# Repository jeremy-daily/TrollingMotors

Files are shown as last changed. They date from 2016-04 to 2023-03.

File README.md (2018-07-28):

# TrollingMotors
A project that runs 2 trolling motors on a boat with multiple microcontrollers on a CAN bus.

## Operation
Pressing the green button lets you change mode with an up and down of the joystick.

The red button stops the motor and sends the system into mode 0, which is off.

### Mode 0: OFF

### Mode 1: Normal 

### Mode 2: Figure 8

### Mode 3: Full

### Mode 4: Calibrate Compass

## Servos
Use the following Arduino pins on the Teensy 3.2

D23 is the left motor.

D16 is the right motor.

The motor controller is a VEX Victor SP that takes inputs generated by the Servo library. The value of 92 is neutral on the controllers.

## CAN Message
This section describes the interpretation and value for each of the CAN messages on the trolling motor system. All nodes are running at 500k CAN with 11-bit IDs.
### Control Message
* ID: 0x700
* Length: 1
* Meaning
  * Bit 0: upButtonState
  * Bit 1: downButtonState
  * Bit 2: leftButtonState
  * Bit 3: rightButtonState
  * Bit 4: pushButtonState
  * Bit 5: doubleClick
  * Bit 6: redButtonState
  * Bit 7: greenButtonState
  
This is the message sent by the Joystick or other controller every 25 ms. 

### Mode Message
* ID: 0x201
* Length: 2
* Meaning
  * Byte 0: number of modes of operation
  * Byte 1: current mode number

This messages is sent by the main controller as an informational message.
  
### Display Message 1
* ID: 0x211
* Length: 8

All bytes are ascii characters to be displayed on the upper left character slots of a 16X2 character display.

### Display Message 2
* ID: 0x212
* Length: 8

All bytes are ascii characters to be displayed on the upper right character slots of a 16X2 character display.

### Display Message 3
* ID: 0x221
* Length: 8
 
All bytes are ascii characters to be displayed on the lower left character slots of a 16X2 character display.

### Display Message 4
* ID: 0x222
* Length: 8

All bytes are ascii characters to be displayed on the lower right character slots of a 16X2 character display.

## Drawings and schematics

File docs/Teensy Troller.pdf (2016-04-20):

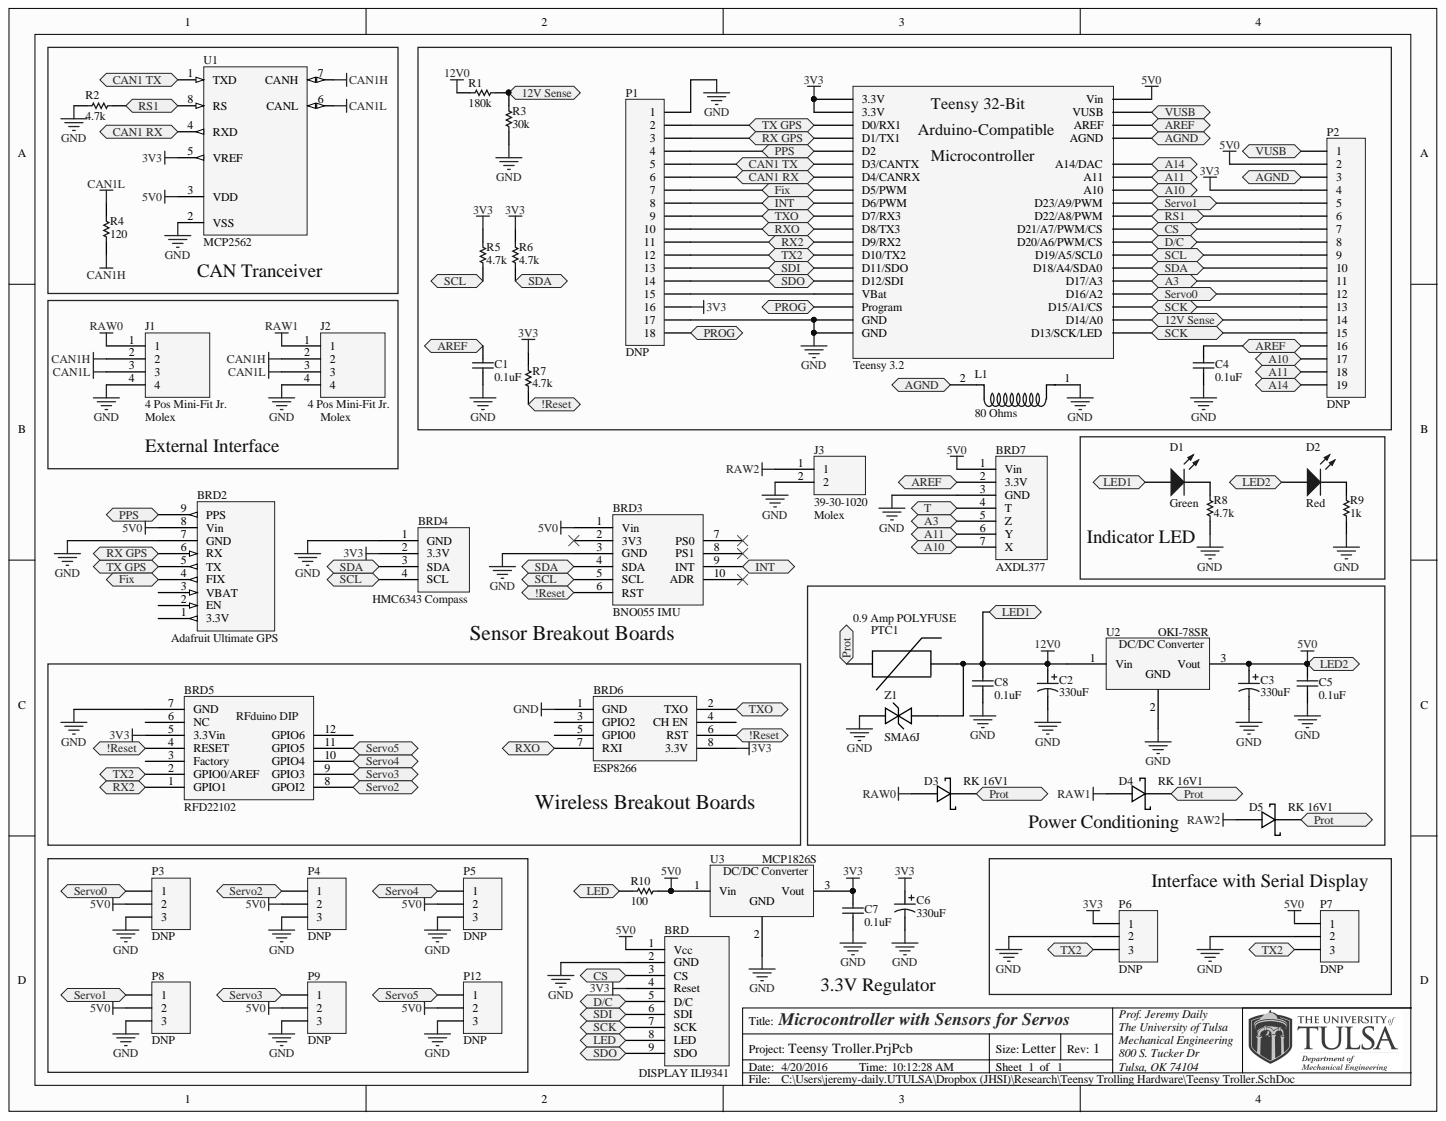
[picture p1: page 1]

4 Pos Mini-Fit Jr.
Molex
External Interface

Interface with Serial Display

GND
Microcontroller with Sensors for Servos
Title:

Prof. Jeremy Daily
The University of Tulsa
Mechanical Engineering
800 S. Tucker Dr

C:\Users\jeremy-daily.UTULSA\Dropbox (JHSI)\Research\Teensy Trolling Hardware\Teensy Troller.SchDoc

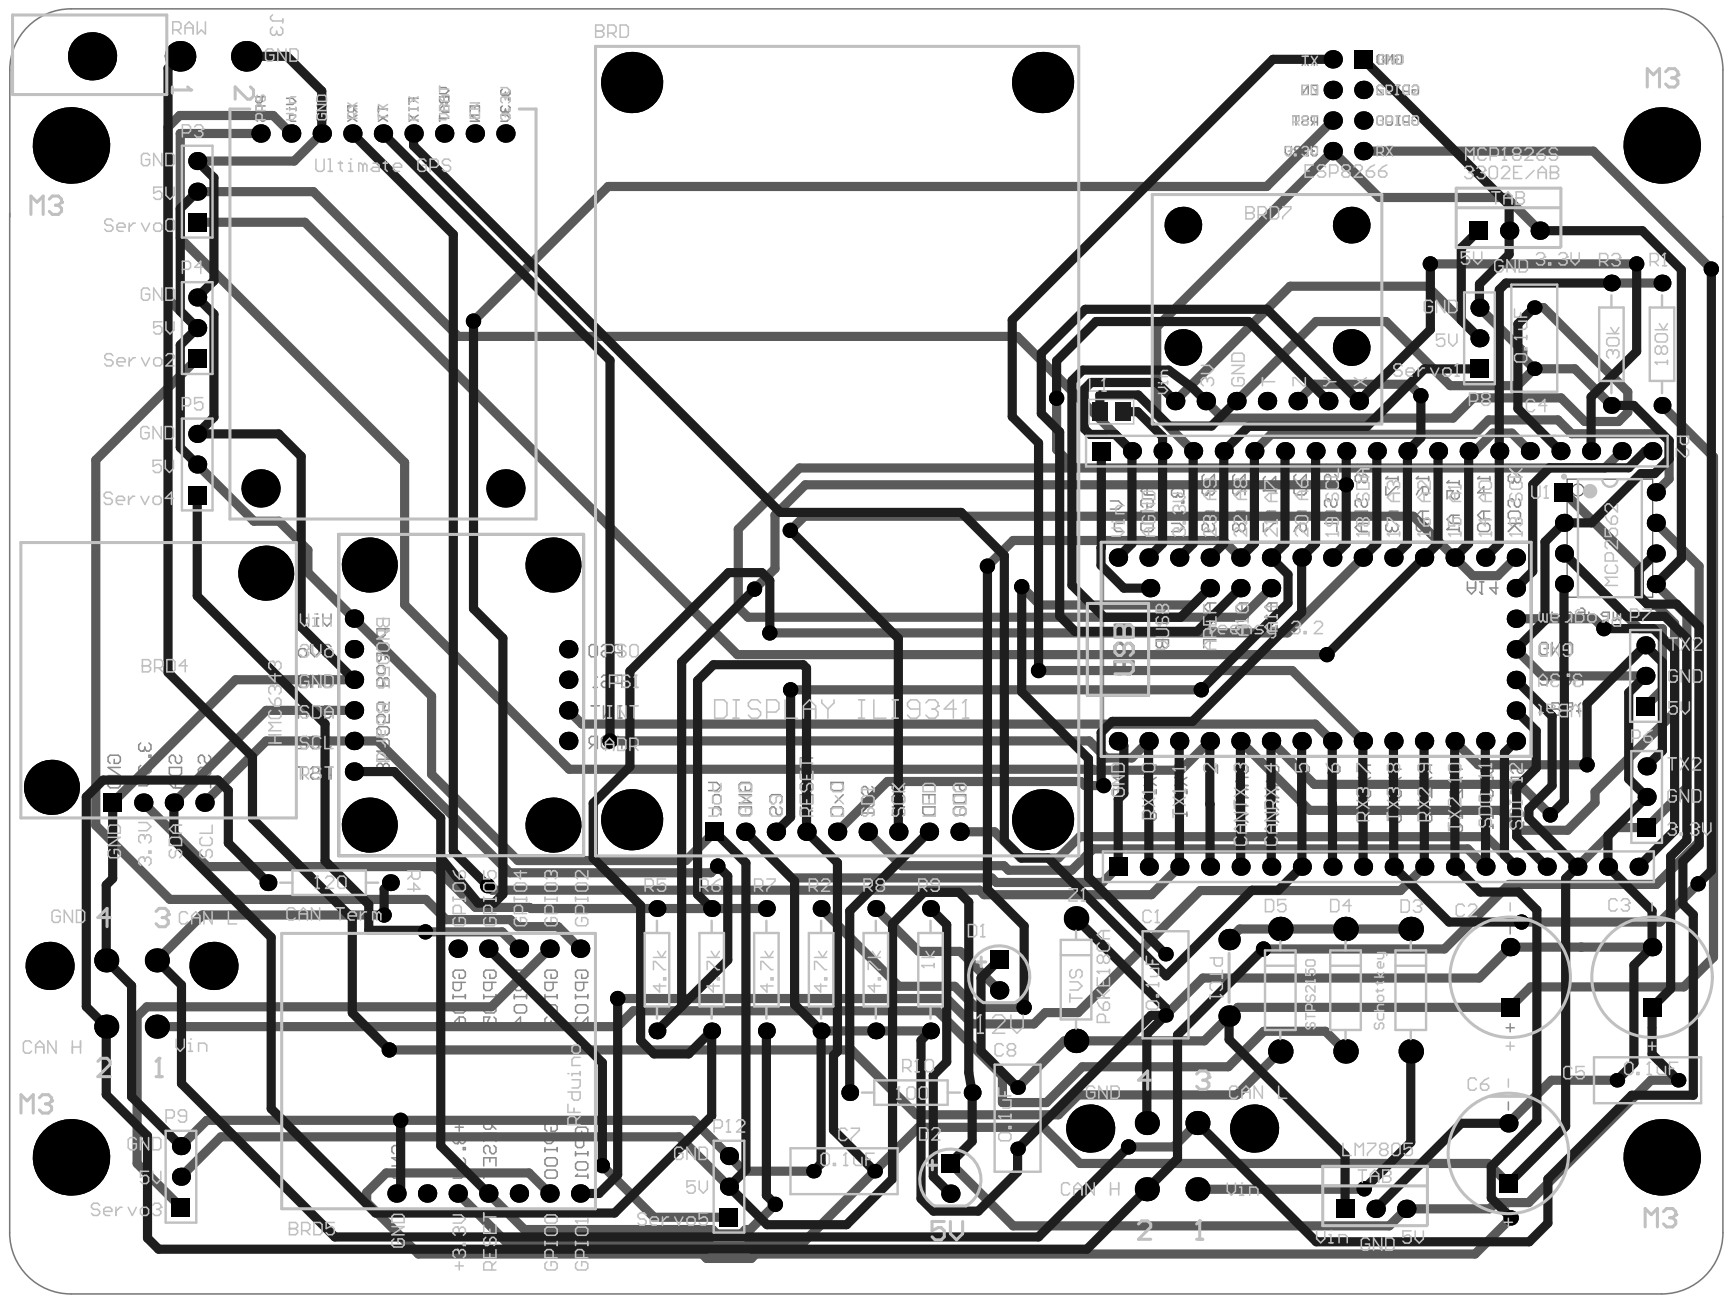
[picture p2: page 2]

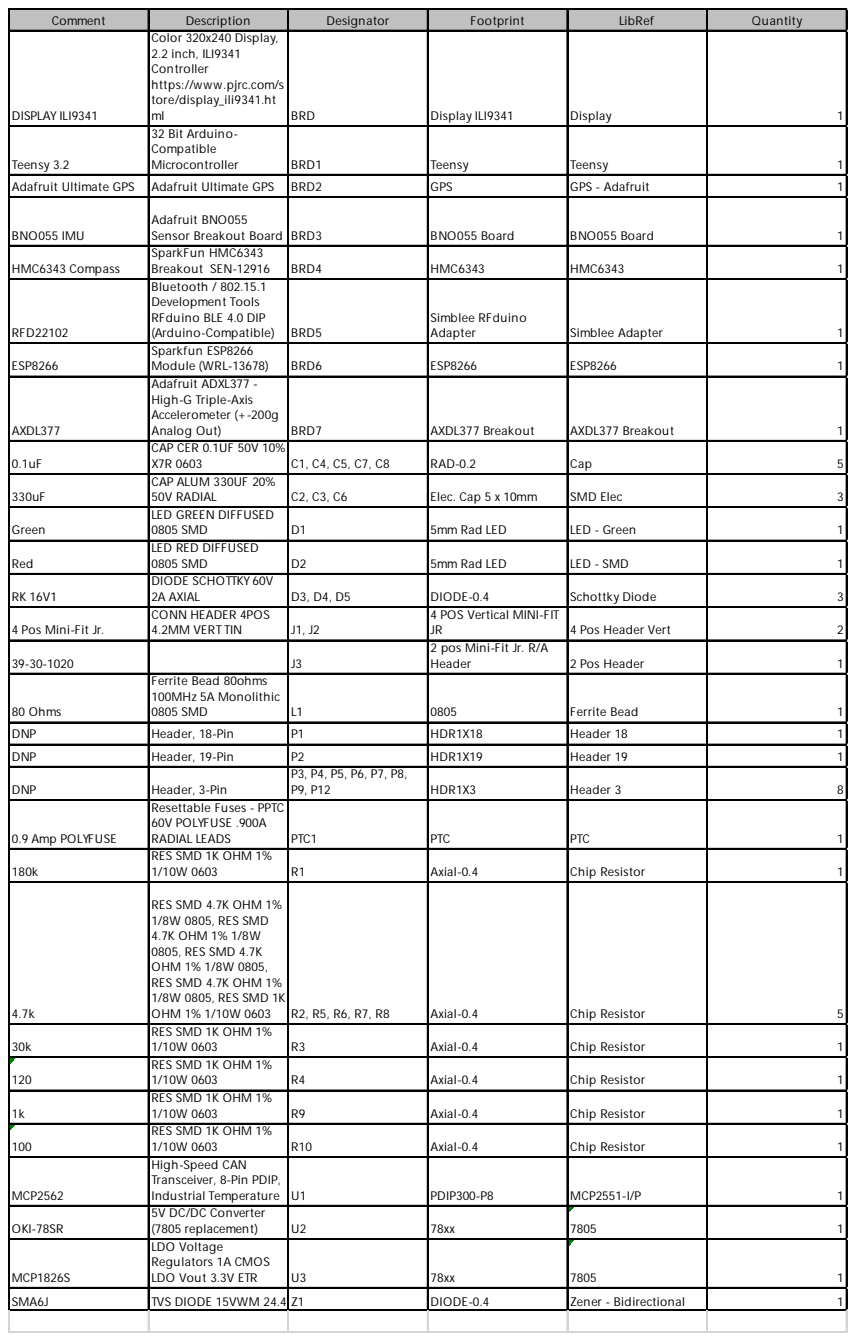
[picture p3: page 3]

Comment | Description | Designator | Footprint | LibRef | Quantity

DISPLAY ILI9341 | Color 320x240 Display, 2.2 inch, ILI9341 Controller https://www.pjrc.com/store/display_ili9341.ht ml | BRD | Display ILI9341 | Display | 1

Teensy 3.2 | 32 Bit Arduino-Compatible Microcontroller | BRD1 | Teensy | Teensy | 1

Adafruit Ultimate GPS | Adafruit Ultimate GPS | BRD2 | GPS | GPS - Adafruit | 1

BNO055 IMU | Adafruit BNO055 Sensor Breakout Board | BRD3 | BNO055 Board | BNO055 Board | 1

HMC6343 Compass | SparkFun HMC6343 Breakout SEN-12916 | BRD4 | HMC6343 | HMC6343 | 1

RFD22102 | Bluetooth / 802.15.1 Development Tools RFduino BLE 4.0 DIP (Arduino-Compatible) | BRD5 | Simblee RFduino Adapter | Simblee Adapter | 1

ESP8266 | Sparkfun ESP8266 Module (WRL-13678) | BRD6 | ESP8266 | ESP8266 | 1

AXDL377 | Adafruit ADXL377 -High-G Triple-Axis Accelerometer (+-200g Analog Out) | BRD7 | AXDL377 Breakout | AXDL377 Breakout | 1

0.1uF | CAP CER 0.1UF 50V 10% X7R 0603 | C1, C4, C5, C7, C8 | RAD-0.2 | Cap | 5

330uF | CAP ALUM 330UF 20% 50V RADIAL | C2, C3, C6 | Elec. Cap 5 x 10mm | SMD Elec | 3

Green | LED GREEN DIFFUSED 0805 SMD | D1 | 5mm Rad LED | LED - Green | 1

Red | LED RED DIFFUSED 0805 SMD | D2 | 5mm Rad LED | LED - SMD | 1

RK 16V1 | DIODE SCHOTTKY 60V 2A AXIAL | D3, D4, D5 | DIODE-0.4 | Schottky Diode | 3

4 Pos Mini-Fit Jr. | CONN HEADER 4POS 4.2MM VERT TIN | J1, J2 | 4 POS Vertical MINI-FIT JR | 4 Pos Header Vert | 2

39-30-1020 | | J3 | 2 pos Mini-Fit Jr. R/A Header | 2 Pos Header | 1

80 Ohms | Ferrite Bead 80ohms 100MHz 5A Monolithic 0805 SMD | L1 | 0805 | Ferrite Bead | 1

DNP | Header, 18-Pin | P1 | HDR1X18 | Header 18 | 1

DNP | Header, 19-Pin | P2 | HDR1X19 | Header 19 | 1
DNP | Header, 3-Pin | P3, P4, P5, P6, P7, P8, P9, P12 | HDR1X3 | Header 3 | 8

0.9 Amp POLYFUSE | Resettable Fuses - PPTC 60V POLYFUSE .900A RADIAL LEADS | PTC1 | PTC | PTC | 1

180k | RES SMD 1K OHM 1% 1/10W 0603 | R1 | Axial-0.4 | Chip Resistor | 1

4.7k | RES SMD 4.7K OHM 1% 1/8W 0805, RES SMD 4.7K OHM 1% 1/8W 0805, RES SMD 4.7K OHM 1% 1/8W 0805, RES SMD 4.7K OHM 1% 1/8W 0805, RES SMD 1K OHM 1% 1/10W 0603 | R2, R5, R6, R7, R8 | Axial-0.4 | Chip Resistor | 5

30k | RES SMD 1K OHM 1% 1/10W 0603 | R3 | Axial-0.4 | Chip Resistor | 1

120 | RES SMD 1K OHM 1% 1/10W 0603 | R4 | Axial-0.4 | Chip Resistor | 1

1k | RES SMD 1K OHM 1% 1/10W 0603 | R9 | Axial-0.4 | Chip Resistor | 1

100 | RES SMD 1K OHM 1% 1/10W 0603 | R10 | Axial-0.4 | Chip Resistor | 1

MCP2562 | High-Speed CAN Transceiver, 8-Pin PDIP, Industrial Temperature | U1 | PDIP300-P8 | MCP2551-I/P | 1

OKI-78SR | 5V DC/DC Converter (7805 replacement) | U2 | 78xx | 7805 | 1

MCP1826S | LDO Voltage Regulators 1A CMOS LDO Vout 3.3V ETR | U3 | 78xx | 7805 | 1

SMA6J | TVS DIODE 15VWM 24.4VZ1 | | DIODE-0.4 | Zener - Bidirectional | 1

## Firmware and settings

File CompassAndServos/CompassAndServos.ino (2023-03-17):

/*
   The Teensy Troller
   A program to implement an autopilot with two trolling motors on a ski boat.

   By Jeremy Daily

   Released under the beer license: If you like it, I'd like to share a beer with you if we ever meet.
*/
#include <TinyGPS++.h> // Used to read the data from the GPS.
#include <FlexCAN.h> // The CAN library for the Teensy used to communicate with the Joystick
#include <i2c_t3.h> // the I2C library that replaces Wire.h for the Teensy 3.2
#include <SFE_HMC6343.h> //Sparkfun's library for the digital compass
#include <Servo.h> // Used to send pulses to the motor controller
#include <EEPROM.h> //used to store compass declination angles and calibration results
#include "BNO055.h"

#define compassOffsetAddress 0
#define CANcompassOffsetAddress 8
double compassOffset; // True - measured, so measured + offset = true

const uint32_t deltaTms = 50; //milliseconds for calculations and output

elapsedMillis broadcastCANtimer; //set up intervals
elapsedMillis waitingForCANtimer;
elapsedMillis debugSerialtimer;
elapsedMillis CANaliveTimer;
elapsedMillis SerialAliveTimer;
elapsedMillis broadcastCANmodeTimer;
elapsedMillis gyroReadingTimer;

double tempHeading = 0;
double compassHeading = 0.0;

const int stopMotorValue = 92;
const int maxRevMotorValue = 8;
const int maxFwdMotorValue = 208;
uint8_t leftMotor = 92;
uint8_t rightMotor = 92;
uint8_t tempLeftMotor = 92;
uint8_t tempRightMotor = 92;

//Initialize the GPS
TinyGPSPlus gps;

SFE_HMC6343 compass; // Declare the sensor object

Servo rightServo;  // create servo object to control a servo
Servo leftServo;  // create servo object to control a servo

static CAN_message_t txmsg, rxmsg;
uint32_t CANTXcount = 0;
uint32_t CANRXcount = 0;
uint32_t ID = 0;

void setup() {
  compassOffset = -23.15299213;
  Wire.begin();
  Serial.println("Welcome to the Teensy Troller. We will get setup first.");

  Serial.print("Starting Bosch BNO055 IMU Sensor... ");
  uint8_t gyroConfig = 0;
  while (gyroConfig != 0b00101100) {
    BNOwrite(BNO055_PAGE_ID_ADDR, 0); // Set to page 0
    delay(40);
    BNOwrite(BNO055_SYS_TRIGGER_ADDR, 0b00100000);
    delay(40);
    BNOwrite(BNO055_SYS_TRIGGER_ADDR, 0b10000000);
    delay(750);

    BNOwrite(BNO055_OPR_MODE_ADDR, OPERATION_MODE_CONFIG); //Set to configuration Mode
    delay(20);
    BNOwrite(BNO055_OPR_MODE_ADDR, OPERATION_MODE_CONFIG); //Set to configuration Mode
    delay(20);
    BNOwrite(BNO055_OPR_MODE_ADDR, OPERATION_MODE_CONFIG); //Set to configuration Mode
    delay(20);
    Serial.println("Done.");

    // Set to use external oscillator
    Serial.print("Setting up for External oscillator... ");
    if (BNOread(BNO055_SYS_CLK_STAT_ADDR) == 0) {
      BNOwrite(BNO055_SYS_TRIGGER_ADDR, 0b10000000);
      Serial.println("BNO055 set to use external oscillator");
    }
    else
    {
      BNOwrite(BNO055_SYS_TRIGGER_ADDR, 0b10000000);
      Serial.println("Problem setting BNO055 to use external oscillator.");
    }
    delay(10);

    Serial.print("Setting up Rate Gyro... ");
    BNOwrite(BNO055_PAGE_ID_ADDR, 1); // Set to page 1
    delay(10);
    BNOwrite(GYRO_CONF_0, 0b00101100); // Set gyroscope to 125deg/s at 23Hz (see pg 28 of datasheet)
    delay(10);
    BNOwrite(GYRO_CONF_1, 0); // Set gyroscope  (see pg 28 of datasheet)
    delay(10);


    Serial.println("Done.");
    Serial.print("Setting up Magnetometer... ");
    BNOwrite(MAG_CONF, 0b00011001); //
    delay(10);
    Serial.println("Done.");

    Serial.print("Setting up Accelerometer... ");
    BNOwrite(ACC_CONF, 0); //
    delay(10);
    Serial.println("Done.");

    Serial.print("Setting up Units... ");
    BNOwrite(BNO055_PAGE_ID_ADDR, 0); // Set to page 0
    delay(10);
    BNOwrite(BNO055_UNIT_SEL_ADDR, 0b00010000); // Set units to M/s^2 Deg/sec, Deg, Deg F
    delay(10);
    Serial.println("Done.");

    Serial.print("Turning on Sensors... ");
    BNOwrite(BNO055_OPR_MODE_ADDR, OPERATION_MODE_AMG); //
    //BNOwrite(BNO055_OPR_MODE_ADDR,OPERATION_MODE_NDOF);//
    delay(10);
    BNOwrite(BNO055_PWR_MODE_ADDR, POWER_MODE_NORMAL);
    delay(10);
    Serial.println("Done.");

    Serial.println("Verifying BNO055 Settings...");
    gyroConfig = getBNO055Status();
  }
  Serial.println("Done with setting up the BNO055.");



  Serial.print("Starting Servos... ");
  rightServo.attach(16);  // attaches the servo on pin 16 to the servo object
  leftServo.attach(23);  // attaches the servo on pin 23 to the servo object
  Serial.println("Done.");

  Serial.print("Starting GPS... ");
  Serial1.begin(9600);
  Serial.println("Done.");
  delay(300);
  Serial.println("Setting GPS to 57600 baud... ");
  Serial1.println("$PMTK251,57600*2C"); //Set Baud Rate to 57600
  delay(100);
  Serial1.flush();
  Serial1.end();
  Serial1.begin(57600);
  Serial.println("Done.");
  
  Serial.println("Setting GPS to update at 5 Hz... ");
  Serial1.println("$PMTK220,200*2C"); //update at 5 Hz
  delay(100);
  Serial1.println("$PMTK300,200,0,0,0,0*2F"); //position fix update to 5 Hz
  Serial.println("Done.");


  Serial.println("Starting Compass... ");
  compass.init();
  byte bSN_LSB = compass.readEEPROM(SN_LSB);
  byte bSN_MSB = compass.readEEPROM(SN_MSB);
  Serial.println("Done.");
  
  Serial.print("Compass Serial Number: ");
  Serial.println(word(bSN_MSB, bSN_LSB));
  compass.writeEEPROM(0x14, 0x00); //Set filter to 0.
  compass.exitStandby();
  delay(100);

  Serial.println("Starting CAN at 250k... ");
  Can0.begin(250000);
  Serial.println("Done.");

  Serial.println("Loading Compass Offsets from EEPROM... ");
  EEPROM.get(compassOffsetAddress, compassOffset);
  Serial.println("Done.");
  delay(1500);
  while (Serial1.available()) gps.encode(Serial1.read());
  delay(50);
  debugDataHeader();
}


void sendCANmessages() {
  if (broadcastCANtimer >= deltaTms) {
    broadcastCANtimer = 0;

    //GPS Messages
    if (gps.speed.isUpdated() ) {
      txmsg.id = 0x43e; //status message
      txmsg.len = 8;
      txmsg.buf[0] = byte( (gps.speed.value() & 0xFF000000) >> 24);
      txmsg.buf[1] = byte( (gps.speed.value() & 0x00FF0000) >> 16);
      txmsg.buf[2] = byte( (gps.speed.value() & 0x0000FF00) >>  8);
      txmsg.buf[3] = byte( (gps.speed.value() & 0x000000FF) >>  0);
      txmsg.buf[4] = byte( (gps.course.value() & 0xFF000000) >> 24);
      txmsg.buf[5] = byte( (gps.course.value() & 0x00FF0000) >> 16);
      txmsg.buf[6] = byte( (gps.course.value() & 0x0000FF00) >>  8);
      txmsg.buf[7] = byte( (gps.course.value() & 0x000000FF) >>  0);
      Can0.write(txmsg);
      CANTXcount++;
    }
  }

  if (broadcastCANmodeTimer >= deltaTms) {
    uint16_t yawRate_int = yawRate * 1000 + 32768;
    broadcastCANmodeTimer = 0;
    txmsg.id = 0x701; //Status message
    txmsg.len = 8;
    txmsg.buf[0] = rightMotor;
    txmsg.buf[1] = leftMotor;
    txmsg.buf[2] = byte( (compass.heading & 0xFF00) >>  8);
    txmsg.buf[3] = byte( (compass.heading & 0x00FF) >>  0);
    txmsg.buf[4] = byte( (yawRate_int     & 0xFF00) >>  8);
    txmsg.buf[5] = byte( (yawRate_int     & 0x00FF) >>  0);
    txmsg.buf[6] = byte( (millis()        & 0xFF00) >>  8);
    txmsg.buf[7] = byte( (millis()        & 0x00FF) >>  0);   
    Can0.write(txmsg);
    CANTXcount++;
  }
}

void readCANMessages( ) {
  Can0.read(rxmsg);
  waitingForCANtimer = 0; //reset the can message timeout
  ID = rxmsg.id;
  if (ID == 0x201) {
    CANaliveTimer = 0;
    tempRightMotor = rxmsg.buf[0];
    tempLeftMotor  = rxmsg.buf[1];
  } 
}

    
void debugDataHeader(){
  if (gps.date.isUpdated())
  {
    Serial.print("GPS Date\t");
    Serial.print(gps.date.year());
    Serial.print("-");
    Serial.print(gps.date.month());
    Serial.print("-");
    Serial.println(gps.date.day());
  }

  if (gps.time.isUpdated())
  {
    Serial.print("GPS Time\t");
    Serial.print(gps.time.hour());
    Serial.print(":");
    Serial.print(gps.time.minute());
    Serial.print(":");
    Serial.println(gps.time.second());
  }

 
  Serial.print("Time [ms]\t");
  Serial.print("Compass [deg]\t");
  Serial.print("GPS Course [deg]\t");
  Serial.print("GPS Speed [mph]\t");
  Serial.print("Yaw Rate [deg/s]\t");
  Serial.print("rightMotor\t");
  Serial.print("leftMotor\t");
  Serial.print("GPS Lat [deg]\t");
  Serial.print("GPS Long[deg]\n");
  
 
}

void debugData() {
  if (debugSerialtimer >= deltaTms) {
    debugSerialtimer = 0;

    Serial.print(millis());
    Serial.print("\t");
    Serial.print(compass.heading/10.0);
    Serial.print("\t");
    Serial.print(gps.course.deg());
    Serial.print("\t");
    Serial.print(gps.speed.mph());
    Serial.print("\t");
    Serial.print(yawRate);
    Serial.print("\t");
    Serial.print(rightMotor);
    Serial.print("\t");
    Serial.print(leftMotor);
    Serial.print("\t");
    Serial.print(gps.location.lat(), 8);
    Serial.print("\t");
    Serial.println(gps.location.lng(), 8);
  }
}

double getCompassHeading() {
  compass.readHeading();
  if ((int(gps.satellites.value()) > 7) && (gps.speed.mph() > 1.0) ){
    tempHeading = gps.course.deg();
  }
  else {
    tempHeading = compass.heading / 10.0 + compassOffset; //local compass
  }
  
  return tempHeading;
}


void getMeasurements() {
  //measure stuff
  if (gyroReadingTimer >= deltaTms) {
    gyroReadingTimer = 0;

    yawRate = BNOgetYawRate();
    compassHeading = getCompassHeading();
  }
  while (Serial1.available()) gps.encode(Serial1.read());
}

void loop() {
  //read stuff
  getMeasurements();

  //send stuff
  sendCANmessages();
  
  //get user input
  readCANMessages();
  
  if (CANaliveTimer > 200) {
    rightMotor = stopMotorValue;
    leftMotor = stopMotorValue;
  }
  else {
    rightMotor = constrain(tempRightMotor, maxRevMotorValue, maxFwdMotorValue);
    leftMotor  = constrain(tempLeftMotor,  maxRevMotorValue, maxFwdMotorValue);
  }
  
  //always send the updates to the motors
  rightServo.write(rightMotor);
  leftServo.write(leftMotor);

  //print stuff
  debugData();
}

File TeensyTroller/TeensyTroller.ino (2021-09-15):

/*
   The Teensy Troller
   A program to implement an autopilot with two trolling motors on a ski boat.

   By Jeremy Daily

   Released under the beer license: If you like it, I'd like to share a beer with you if we ever meet.
*/
#include <TinyGPS++.h> // Used to read the data from the GPS.
#include <FlexCAN.h> // The CAN library for the Teensy used to communicate with the Joystick
#include "SPI.h" //Serial Peripherial Interface
#include  <i2c_t3.h> // the I2C library that replaces Wire.h for the Teensy 3.2
#include <SFE_HMC6343.h> //Sparkfun's library for the digital compass
#include <Servo.h> // Used to send pulses to the motor controller
#include <EEPROM.h> //used to store compass declination angles and calibration results

float turnRate = 0.5; //degrees per second
int turnTime = 100;
int changeLimit = 2;

#define compassOffsetAddress 0
#define CANcompassOffsetAddress 8
double compassOffset;// True - measured, so measured + offset = true

//PID Gain Constants. Tune these for best results.
//Field Test result worked with angleK = 4, angleI = .3, angleD = 25. Determined on 20 July 2016 on Skiatook Lake
//Field Test result worked with angleK = 8, angleI = .3, angleD = 30. Determined on 25 July 2018 on Jackson Lake
double angleK = 8;
double angleI = .3;
double angleD = 32;

//These still need tuned, but they seem to work.
double speedK = .1;
double speedI = .3;
double speedD = 0;

int feedforward = 10;
int feedforwardSpeed = 29;

//Set up the Kalman filter to smooth the data from the Compass and Rate Gyro.
// These must be defined before including TinyEKF.h
#define N 3     // three state values: yawAngle, yawRate, speed
#define M 4     // Four measurements: compassHeading, rateGyro, GPS speed, CAN Speed

//Call the Extended Kalman filter to set up sensor fusion for the rate gyro and the compass.
#include <TinyEKF.h>

//declare this here so it can be used in the Fuser model.
double deltaT = 0.05;

class Fuser : public TinyEKF {

  public:

    Fuser()
    {
      // We approximate the process noise using a small constant
      this->setQ(0, 0, .0001);
      this->setQ(1, 1, .0001);
      this->setQ(2, 2, .0001);
      this->setQ(3, 3, .0001);

      // Same for measurement noise (MxM diagnonal matrix assumes no covariance)
      this->setR(0, 0, 1.5); //Varianance of the noise from the Compass (deg)^2
      this->setR(1, 1, .002); //Variance of the noise from the rate gyro (deg/s)^2
      this->setR(2, 2, .05); //Noise from the GPS speed
      this->setR(3, 3, .05); //Noise from the second GPS

    }

  protected:

    void model(double fx[N], double F[N][N], double hx[M], double H[M][N])
    {
      // Process model is f(x) = x
      fx[0] = this->x[0] - this->x[1] * deltaT; //degrees
      fx[1] = this->x[1]; // deg/s
      fx[2] = this->x[2]; // from 1 GPS
      //fx[3] = this->x[2]; // from the other GPS


      //Process model Jacobian
      F[0][0] = 1; //df[0]/dx[0]
      F[0][1] = deltaT; //df[0]/dx[1]
      F[1][0] = 0; //df[1]/dx[0]
      F[1][1] = 1; //df[1]/dx[1]

      F[2][2] = 1;
      F[2][3] = 0;//deltaT*21.9545;
      F[3][2] = 0;
      F[3][3] = 1;

      // Measurement function
      hx[0] = this->x[0]; // Yaw Angle from previous state
      hx[1] = this->x[1]; // yaw Rate from previous state
      hx[2] = this->x[2]; // Speed from previous state
      hx[3] = this->x[2]; // Speed acceleration from previous state

      // Jacobian of measurement function
      H[0][0] = 1;       // Yaw Angle from previous state
      H[1][1] = 1;       // yaw Rate from previous state
      H[2][2] = 1;
      H[3][3] = 1;

    }
};

Fuser ekf;

double ekfYawAngle;
double ekfYawRate;
double ekfSpeed;
//double ekfAccel;

char topLine[17];
char botLine[17];

double gyroScaleFactor = 0.003814697265625; //Set to 125deg/s / 2^15
//double gyroOffset = -0.122513335; //Used to zero out the rate gyro when it is still. Uses a longterm average.
double gyroOffset = -0.099003911;//Used to zero out the rate gyro when it is still. Uses a longterm average.

double biasSetting = 1.00; // adjust this value to make the boat go straight in full mode. This the compensation coefficent for the right motor

uint8_t headingCount = 0;
double headingSum = 0;
double CANheadingSum = 0;

#include "BNO055.h"


const int memorySize = 2400;
int32_t differenceList[2400];
int32_t differenceSpeedList[2400];

double accelX = 0;

const uint32_t deltaTms = 50; //milliseconds for calculations and output
const uint32_t modeDisplayPeriod = 147;

double yawOffset = 0;
double CANcompassOffset = 0;
boolean needsRealigned  = true;
boolean needsToPrint = true;

double CANheading;
double CANcompassHeading;
double headerValue;
double headingReading;
double totalTurn = 0;
double lastAngle = 0;
double targetAngle = 0;
double endAngle = 0;
double startAngle = 0;

double omega = 0;
double motorInput = 0;

double gpsSpeed = 0;
double gpsAngle = 0;
byte gpsSats  = 0;
byte gpsFix   = 0;
int dist;
double distK = 0.2;

const int stopMotorValue = 92;
const int maxRevMotorValue = 8;
const int maxFwdMotorValue = 208;

#define DISPLAY_PERIOD 197
elapsedMillis upperLeftTimer;
elapsedMillis upperRightTimer;
elapsedMillis lowerLeftTimer;
elapsedMillis lowerRightTimer;

elapsedMillis calculateMotorOutputTimer; // this is interrupt based
elapsedMillis broadcastCANtimer; //set up intervals
elapsedMillis waitingForCANtimer;
elapsedMillis debugSerialtimer;
elapsedMillis modeDisplayTimer;
elapsedMillis modeChangeTimer;
elapsedMillis CANaliveTimer;
elapsedMillis SerialAliveTimer;
elapsedMillis speedSettingTimer;
elapsedMillis broadcastCANmodeTimer;
elapsedMillis courseSettingTimer;
elapsedMillis gyroReadingTimer;

elapsedMillis fig8timer;
elapsedMillis turnTimer;
elapsedMillis turnUpdateTimer;
elapsedMillis resetCompassTimer;

const int speedSetTime = 150; //set how quickly the speed changes.
const int courseSetTime = 150; //set how quickly the Course inputs changes.

boolean mode1started = false;
boolean mode2started = false;
boolean mode3started = false;
boolean mode4started = false;
boolean mode5started = false;
boolean mode6started = false;
boolean mode7started = false;

byte mode = 0;
byte currentMode = 0;
byte numberOfModes = 5; //This limits the number of displayed modes.
byte fig8phase = 0;

boolean rightButtonState = LOW;
boolean leftButtonState = LOW;
boolean downButtonState = LOW;
boolean pushButtonState = LOW;
boolean upButtonState = LOW;
boolean greenButtonState = LOW;
boolean redButtonState = LOW;


// Jackson Lake
double fixPointLat = 43.84825516;
double fixPointLon = -110.6231537;
double distanceToFixPoint = 0;
double courseToFixPoint = 0;
double integral = 0;

int diffIndex = 0;
int diffSpeedIndex = 0;

double difference = 0;
double speedDifference = 0;
double goalAngle = 0;
double turnGoal = 0;
double goalSpeed = 0;
double turnSetting = 0;
double tempHeading = 0;

int speedSetting;
int angleSetting;
int previousAngleSetting;
int speedAdjust;
int previousSpeedAdjust;

double compassHeading = 0.0;
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

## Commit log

2015-07-11 Added button debouncing to Joystick
2015-07-13 Added Compass and Motor Driver Sketches
    Incorporated GPS signals and Voltage Readings that come over CAN.
2015-07-15 Added PID strategy with feed-forward
    Use bitshifting to get fractional gains.
2015-07-17 Modified for PID. Added Full Trottle. Better Serial.
2015-07-18 Update with tenths of a degree
    Added files after sea trial 1
    [Bus Traffic trolling 180 7-17-2015 10-46-28 am.xlsx, Bus Traffic trolling 180 7-17-2015 12-44-52 pm.xlsx, Bus Traffic trolling fig8 fail 7-17-2015 10-31-45 am.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]
2015-07-30 Pre Yellowstone 2015
    [Bus Traffic trolling 180 7-17-2015 12-44-52 pm.xlsx, SerialDataLog Attempt Straight plus full swings.xlsx]
2015-08-05 Post Yellowstone - Working System, Not Optimal
    [Turn 180 K50 I6 D-100 7-31-2015 3-08-18 pm.csv, Turn 180 K50 I6 D-100 7-31-2015 3-08-18 pm.xlsx, Turn 90s K20 I6 D-100 7-31-2015 3-15-55 pm.csv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]
2016-04-20 Posted Altium files for new controller board.
    [Hammond 1554H Template.PcbDoc, Teensy Troller.PcbDoc, Teensy Troller.PrjPcb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]
2016-06-11 Sensors Displayed on TFT
    Have IMU data and Compass Data displayed
2016-06-12 Added CAN support for GPS and Buttons
2016-06-19 Made Joystick Interrupt Based
    Improved performance to only execute tasks on interrupt.
2016-06-25 Mode Ready for Testing
    Have PID loop and checed the Motors
2016-06-27 Testing day 1
    [TeensyTroller Test 1.xlsx]
2016-06-27 Added more general servo outputs
2016-06-28 Adjusted motor stops
2016-07-04 Added Calibration Modes, Switched to Compass
    [Hammond 1554H Template.PcbDoc]
2016-07-04 Fixed Integrator, added mode 7
    Added mode 7 to do a frequency sweep to get model data.
    [TeensyTroller.ino]
2016-07-13 Added Skiatook Trial Data
    Try new Sketch
    [Frequency Sweep Data.xlsx, Left Turn Step.xlsx, RIght Step input.xlsx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]
2016-07-17 Added more data files
    Second lake test
    [HIgh Gains.xlsx, UnityGain.xlsx, left step new gains.xlsx]
2016-07-19 Got Kalman Filtering to work.
    [Static Measurements.xlsx]
2016-07-20 Added Speed to the EKF
    Made rate gyro startup more robust
2016-07-21 Successful Field Trial
    Keep this for a successful manual mode.
    [DrivingToMarcos..xlsx, ThisWorks-we can use these gains.xlsx]
2016-07-22 Added papers and Plotted Data
    [Compass.csv, DrivingToMarcos..xlsx, ThisWorks-we can use these gains.xlsx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]
2016-08-03 Catching Fish in Yellowstone
    [Figure8 in Yellowstone - should be good.xlsx, Yellowstone 180.xlsx, Yellowstone Straight.xlsx]
2016-08-07 Data after Yellowstone 2016
    Has all the data from maneuvers needed to catch 119 fish.
    [Figure 8 again after tweak - seems good.xlsx, Figure8 in Yellowstone - should be good.xlsx, Step right 20 deg-Yellowstone2016.csv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]
2016-11-29 Added Libraries and Kalman Exampls
    [gps.csv, results.csv]
2017-07-23 Updated relay to monitor engine speed
2017-07-29 Updated for charge relay
2017-08-08 Fixed discontinutity in turns
    [TeensyTroller.ino]
2018-06-26 Fixed joystick with additional buttons
    [JoystickAndDisplay.ino, TeensyTroller.ino]
2018-07-03 Added PID parameter updates
2018-07-06 added teensy only GPS
2018-07-25 revert to known working state before serial
    [JoystickAndDisplay.ino, TeensyTroller.ino]
2018-07-25 Revert "Fixed turn rate"
    This reverts commit 54492300bed9f6a4bb53d489b8c4c245bab31bb2.
    [TeensyTroller.ino]
2018-07-28 cleaned Files
    [Bus Traffic trolling 180 7-17-2015 10-46-28 am.xlsx, Bus Traffic trolling 180 7-17-2015 12-44-52 pm.xlsx, Bus Traffic trolling fig8 fail 7-17-2015 10-31-45 am.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]
2018-07-28 Mode Switching on Main Controller
